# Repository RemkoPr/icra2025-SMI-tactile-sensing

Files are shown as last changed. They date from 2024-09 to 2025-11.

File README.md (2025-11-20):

# ICRA2025: Self-Mixing Laser Interferometry for Robotic Tactile Sensing

[[Main Paper](https://arxiv.org/abs/2502.15390), [Follow-up](https://arxiv.org/abs/2504.13711)] The source files in this repo are provided as-is, additional support for recreating the design can be requested, see contact information below.

# Repo structure

`code > arduino` contains readout firmware for the fingertips. In the paper, the SMI fingertip was read by an Arduino UNO or our [Halberd coupling](https://github.com/RemkoPr/airo-halberd/tree/main), the microphone was read by an Arduino MKR 1000 WiFi.

`code > python` contains code to communicate with the readout microcontrollers from a remote machine over a serial connection.

`data` contains the data files used in the paper.

`mechanical-design` contains SolidWorks design files for the structural parts of the fingertips.

`pcb-design` contains KiCad design files for the PCBs.

For the spectrogram classificatier used in the [follow-up paper](https://arxiv.org/abs/2504.13711), see [this repo](https://github.com/tlpss/ast).

# User Guide

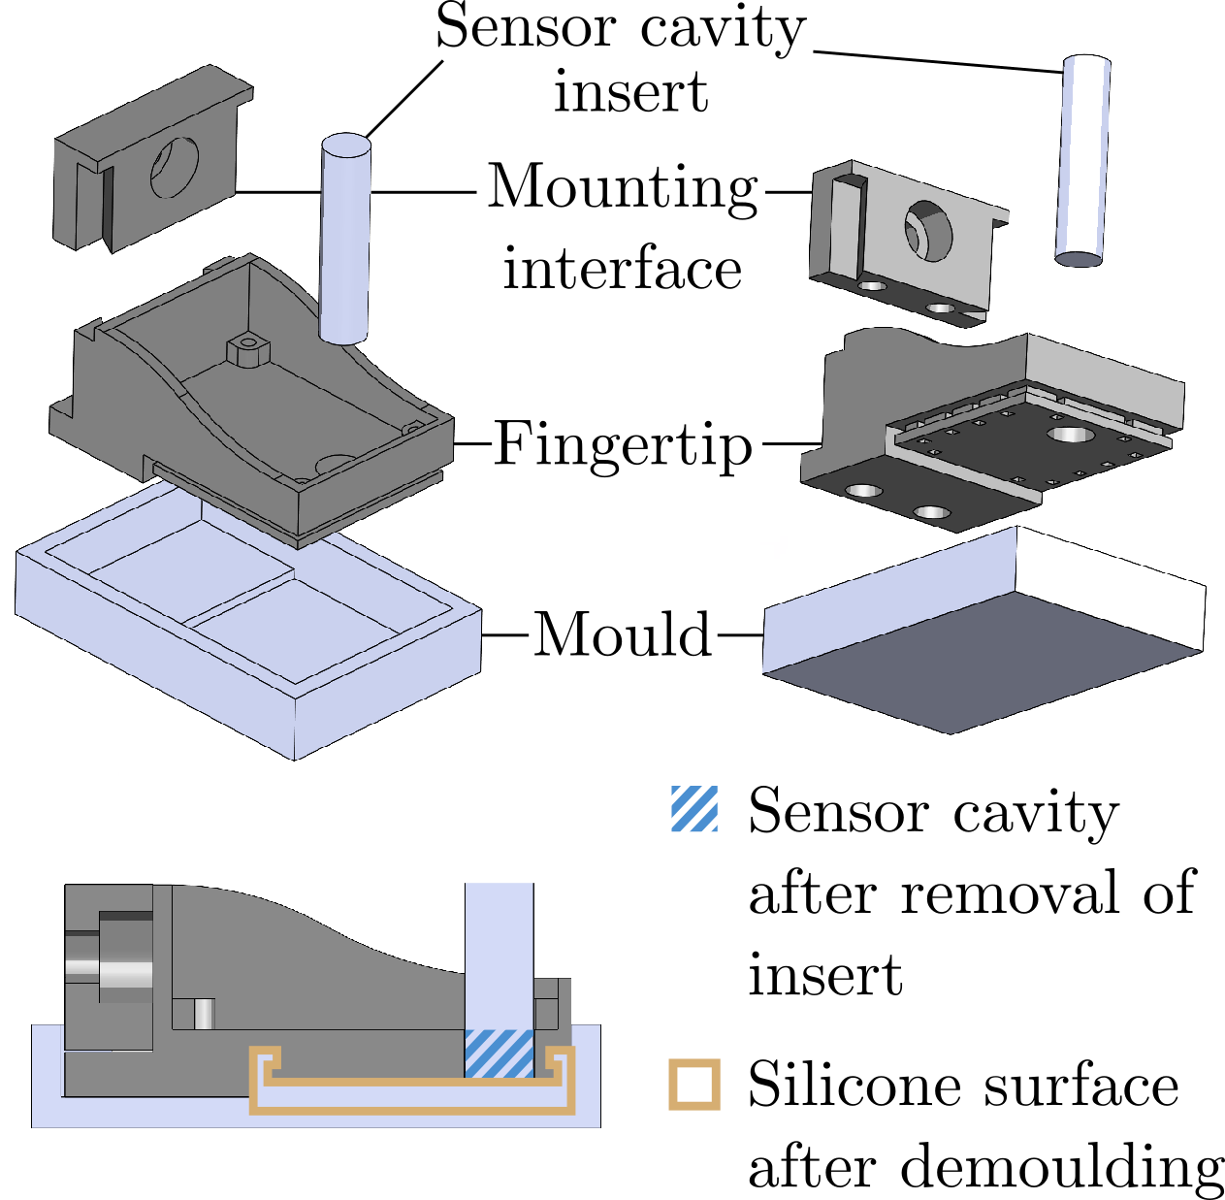
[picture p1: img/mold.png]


The info in this paragraph is relevant for both the microphone and the laser.

Order the PCBs (`pcb-design > microphone` and `pcb-design > laser`) from your favorite manufacturer, refer to the BOM in the main directory of this repo for required parts.
Print the .stl files in `mechanical-design`.
The process of moulding the silicone contact surface is illustrated by the graphic on the right. To keep the "sensor cavity insert" in the right position, fix it with hot glue. It is recommended to attach the "mounting interface" to the fingertip while curing, so that the silicone has less chance to leak.

<BR CLEAR="all">

## Microphone specifics

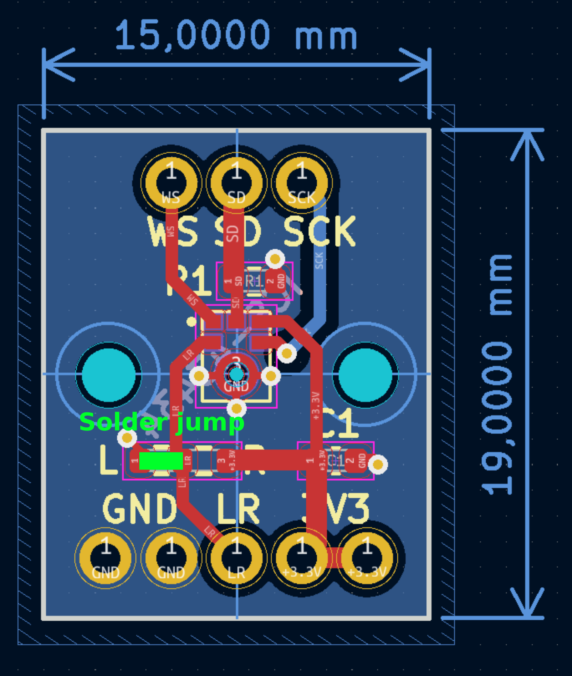
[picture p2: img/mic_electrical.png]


On the PCB, you must set the microphone to either by left or right channel, this will determine during which phase of the I2S communication cycle the microphone sends its data. Do this by soldering a bridge as indicated on the image (the readout code in this repo was tested for left channel, so with a bridge soldered from the middle pad to the L pad).

The MKR1000 firmware (`code > arduino > microphone`) was used for the paper, the wiring is explained in the top rows of the `I2S_MKR1000.ino` file. The `I2S_ArduinoNanoBLE_16kHz` is a first attempt at a readout implementation for the Arduino Nano 33 BLE, for which the standard I2S library isn't implemented.

To run the Python code (`code > python`), run `python -m code.python.communication.readers.micmanip_serial_reader`. The data is published to a CycloneDDS topic MicManip. You can visualise it using `python -m code.python.visualisation.visualisers.micmanip_spectrogram_visualiser MicManip`
<BR CLEAR="all">

## Laser specifics

⚠️ The SMI circuit has a ~5 min warmup time before microvibrations can be measured.

The readout frequency when read with an Arduino UNO was 3.7kHz, and 18kHz with our [Halberd coupling](https://github.com/RemkoPr/airo-halberd/tree/main) (or equivalently with an Arduino Nano 33 BLE, same microcontroller unit). When using higher readout frequency, turn off the 2kHz anti-aliasing filter with the on-PCB slide switch.

To run the Python code (`code > python`), run `python -m code.python.communication.readers.laserslip_serial_reader`. The data is published to a CycloneDDS topic LaserSlip. You can visualise it using `python -m code.python.visualisation.visualisers.laserslip_spectrogram_visualiser LaserSlip`

# Contact

For support regarding the design files in this repo, raise an issue or contact me at remko.proesmans@ugent.be.

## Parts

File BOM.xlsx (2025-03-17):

Mechanical | Qty per fingertip | Purpose
3D filament (e.g. PLA) |  | Mechanical parts
Castable Silicone 50A hardness (e.g. Silicone Addition colorless 50 by Silicones and More) |  | Silicone contact surface
M3 threaded heat-set inserts | 2 | Inserted into the mounting interface
M5x14 bolt | 1 | Mounting fingertip to Robotiq gripper
M2x6 bolts | 4 | Attaching PCBs to printed fingertips
Electrical | Qty per fingertip | Item | PCB designation
Microphone
ICS43434 | 1 | Microphone
100 nF 0603 capacitor | 1
100 kOhm 0603 resistor | 1
Laser
ADL-65075TL | 1 | Laser | D1
ncr320zx | 1 | Constant current source | Q1
ADA4000-1 | 3 | Amplifiers and filters | TIA1, SA1, AA1
MCP3201-BI/SN | 1 | ADC | ADC1
MCP1541T-I_TT | 1 | ADC reference voltage | U2
JS202011SCQN | 1 | Switch | S1
TPS7A3901DSCR | 1 | Voltage regulator | LDO1
MEA1D2409SC | 1 | Voltage regulator | U3
82223C | 2 | 22 µH inductor | L1, L2
5 pF 0603 capacitor | 1 | TIA gain stabilising | C1
100 nF 0603 capacitor | 10 |  | C2, C3, C7, C8, C9, C10, C13, C14, C15, C19
1 µF 0603 capacitor | 1 |  | C20
2,2 µF 0603 capacitor | 3 |  | C4, C5, C6
10 µF 0603 capacitor | 4 |  | C11, C12, C16, C17
500 Ohm 0603 resistor | 1 |  | R5
800 Ohm 0603 resistor | 2 |  | R9, R10
6,8 kOhm 0603 resistor | 1 |  | R4
10 kOhm 0603 resistor | 3 |  | R3, R13, R14
15 kOhm 0603 resistor | 1 |  | R6
32,4 kOhm 0603 resistor | 1 |  | R7
39 kOhm 0603 resistor | 1 | TIA gain | R2
42,2 kOhm 0603 resistor | 1 |  | R8

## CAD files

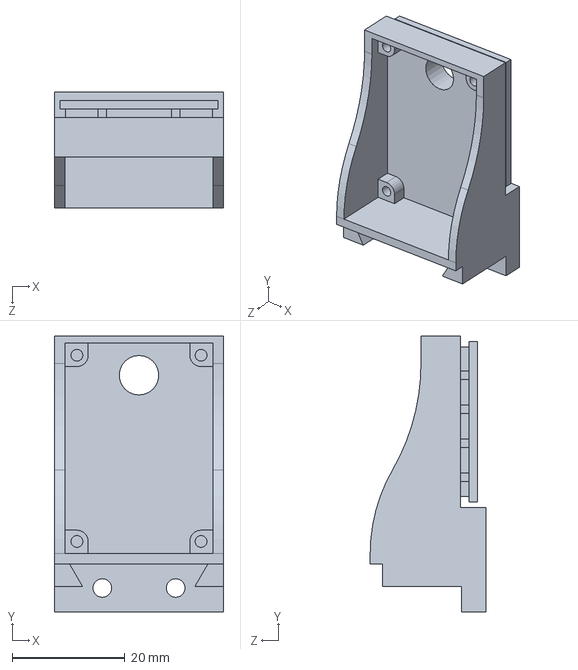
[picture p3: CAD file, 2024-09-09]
mechanical-design/laser/fingertip.SLDPRT
30.0 x 48.9 x 20.5 mm

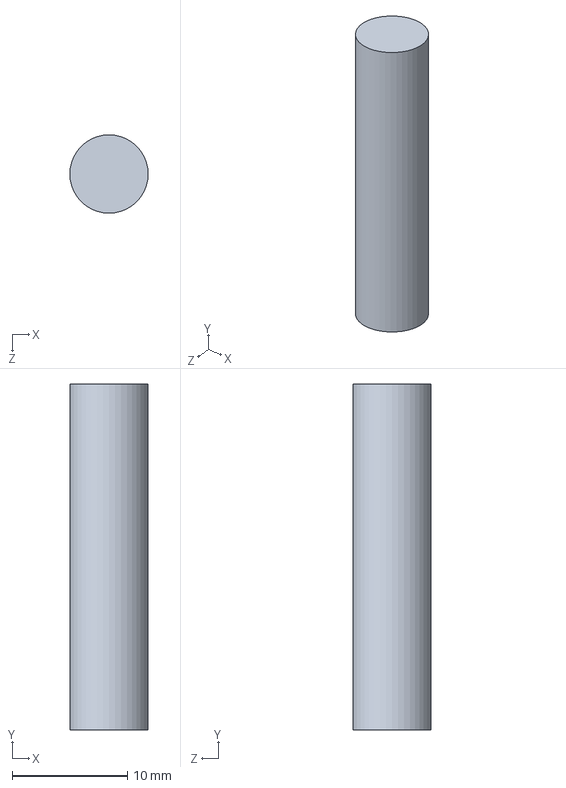
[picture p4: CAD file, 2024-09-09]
mechanical-design/laser/sensor_cavity_insert.SLDPRT
6.80 x 30.0 x 6.80 mm

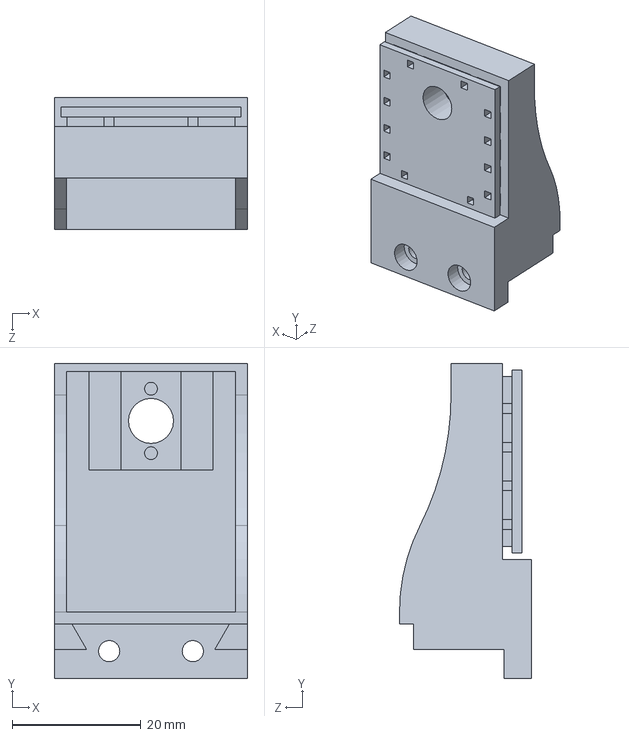
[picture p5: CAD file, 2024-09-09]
mechanical-design/microphone/fingertip.SLDPRT
30.0 x 48.9 x 20.5 mm

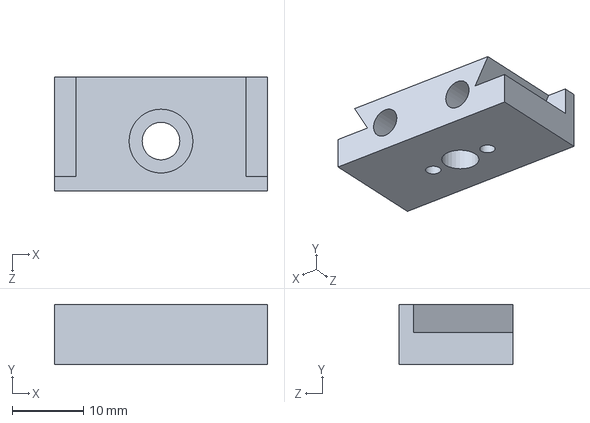
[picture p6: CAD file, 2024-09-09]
mechanical-design/laser/mounting_interface.SLDPRT
30.0 x 8.50 x 16.0 mm

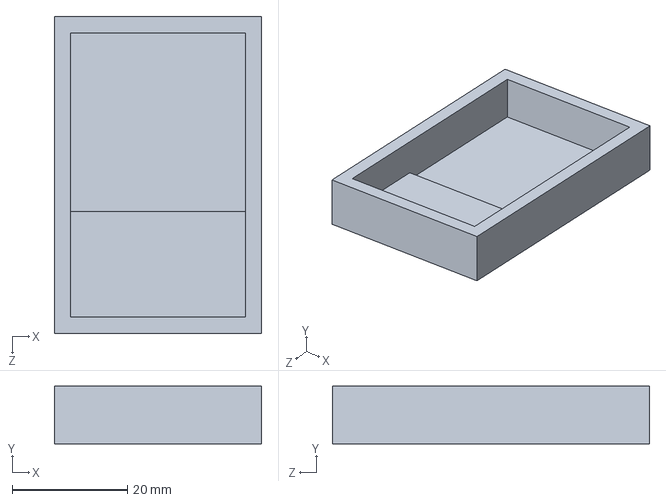
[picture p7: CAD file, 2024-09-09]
mechanical-design/laser/mould.SLDPRT
36.0 x 10.0 x 55.0 mm

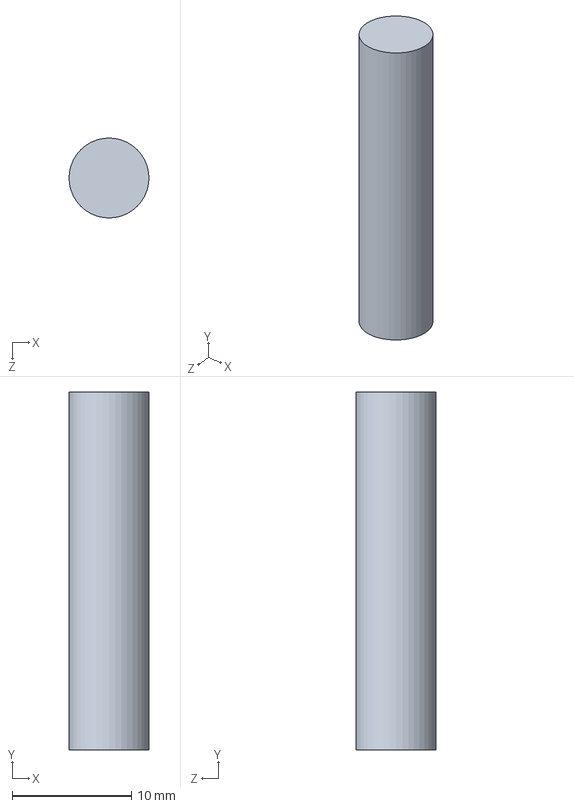
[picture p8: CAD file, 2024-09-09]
mechanical-design/microphone/sensor_cavity_insert.SLDPRT
6.70 x 30.0 x 6.70 mm

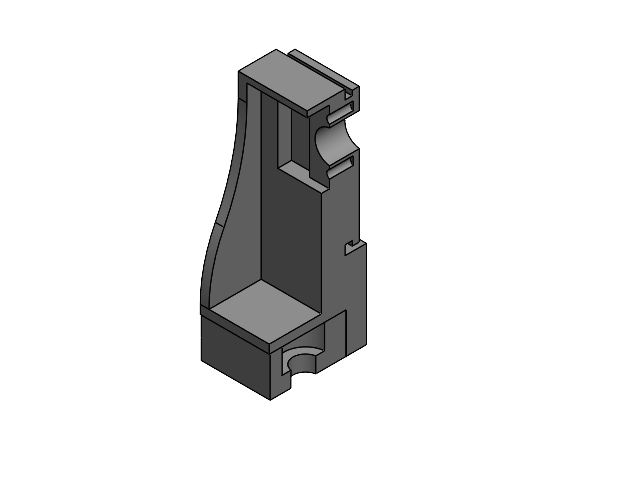
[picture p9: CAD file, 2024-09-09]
mechanical-design/microphone/assembly.SLDASM
fingertip_silicone
base

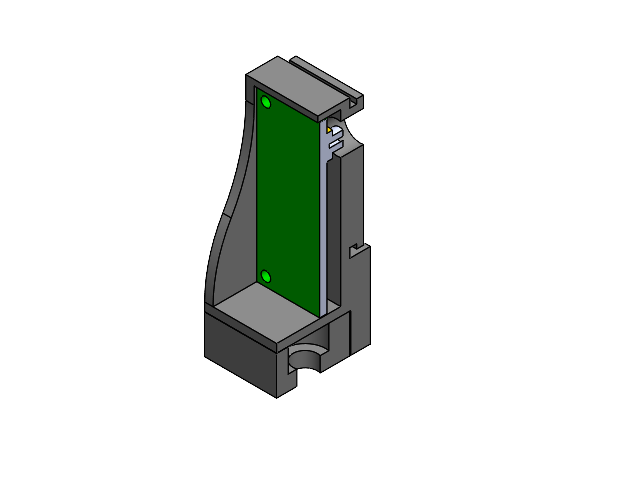
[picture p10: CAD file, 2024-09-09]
mechanical-design/laser/assembly.SLDASM
fingertip
base
PCB

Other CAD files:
mechanical-design/microphone/mounting_interface.SLDPRT
mechanical-design/microphone/mould.SLDPRT
mechanical-design/laser/fingertip.STL
mechanical-design/laser/mould.STL
mechanical-design/laser/mounting_interface.STL
mechanical-design/laser/sensor_cavity_insert.STL
mechanical-design/microphone/fingertip.STL
mechanical-design/microphone/mould.STL
mechanical-design/microphone/mounting_interface.STL
mechanical-design/microphone/sensor_cavity_insert.STL

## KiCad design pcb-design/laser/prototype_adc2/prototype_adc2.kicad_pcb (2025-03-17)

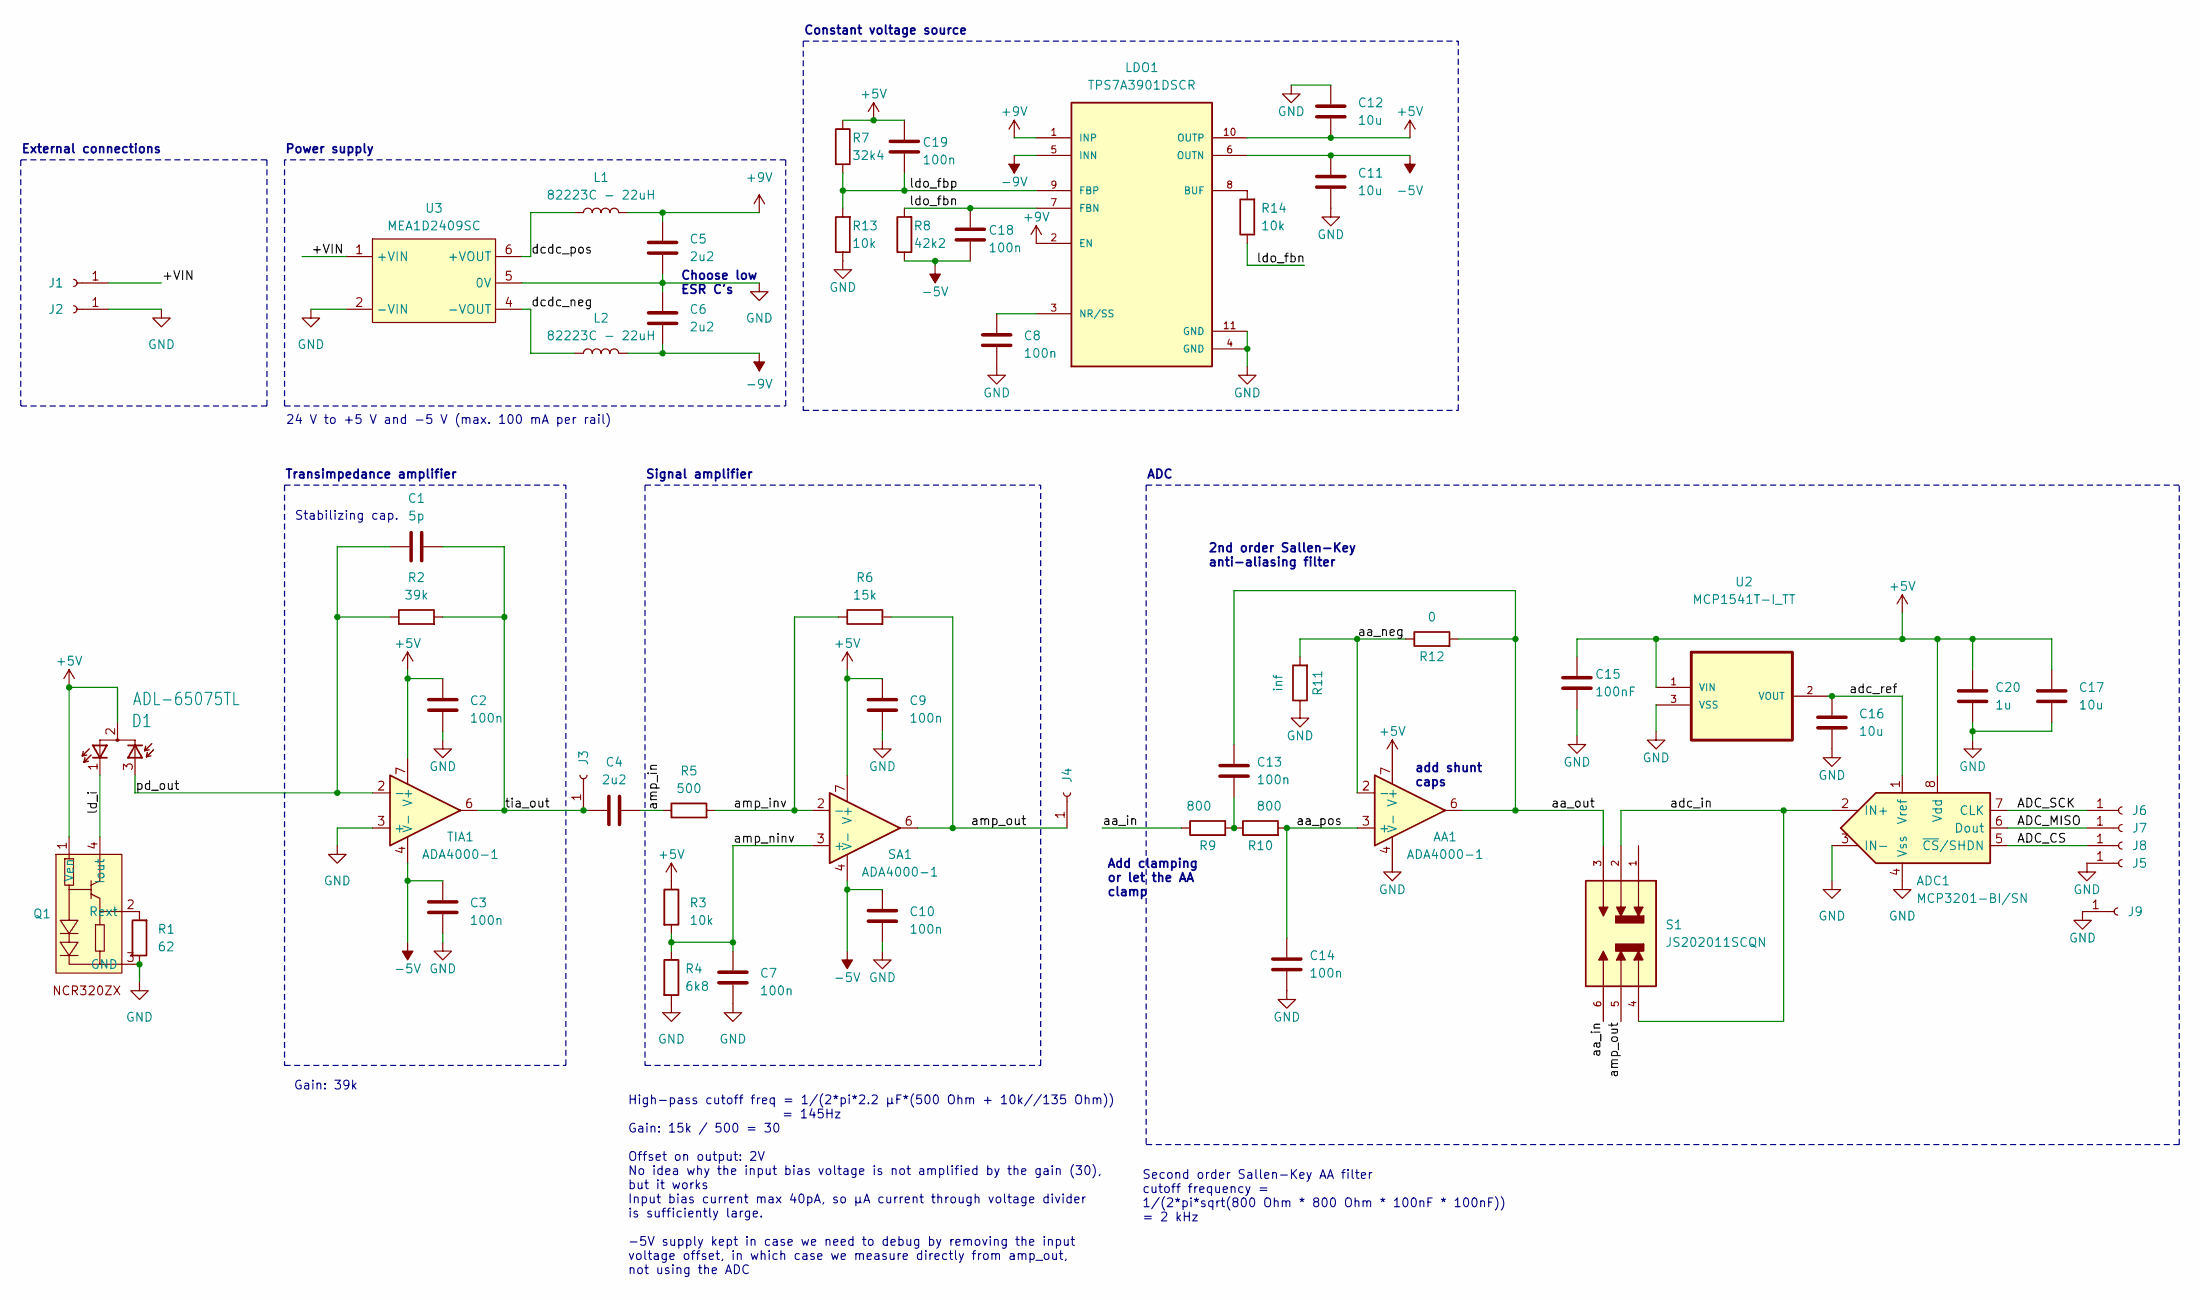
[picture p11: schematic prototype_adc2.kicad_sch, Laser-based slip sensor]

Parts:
AA1: ADA4000-1; ada4000-SOIC127P600X175-8N
ADC1: MCP3201-BI/SN; SOIC127P600X175-8N
C1: 5p; C_0603_1608Metric
C2, C3, C7, C8, C9, C10, C13, C14, C18, C19: 100n; C_0603_1608Metric
C4, C5, C6: 2u2; C_0603_1608Metric
C11, C12, C16, C17: 10u; C_0603_1608Metric
C15: 100nF; C_0603_1608Metric
C20: 1u; C_0603_1608Metric
D1: ADL-65075TL; TO18L
J1, J2, J3, J4, J5, J6, J7, J8, J9: Conn_01x01_Socket; HOLE
L1, L2: 82223C - 22uH; 8200
LDO1: TPS7A3901DSCR; SON50P300X300X80-11N
Q1: TRANS_BCP56-16TX
R1: 62; R_0603_1608Metric
R2: 39k; R_0603_1608Metric
R3, R13, R14: 10k; R_0603_1608Metric
R4: 6k8; R_0603_1608Metric
R5: 500; R_0603_1608Metric
R6: 15k; R_0603_1608Metric
R7: 32k4; R_0603_1608Metric
R8: 42k2; R_0603_1608Metric
R9, R10: 800; R_0603_1608Metric
R11: inf; R_0603_1608Metric
R12: 0; R_0603_1608Metric
S1: JS202011SCQN; SW_JS202011SCQN
SA1: ADA4000-1; ada4000-SOIC127P600X175-8N
TIA1: ADA4000-1; ada4000-SOIC127P600X175-8N
U2: MCP1541T-I_TT; SOT96P237X112-3N
U3: MEA1D2409SC

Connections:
+5V: AA1.7 (V+), ADC1.8 (Vdd), C2.1, C9.1, C12.2, C15.1, C17.1, C19.1, C20.1, D1.2 (CMONI), LDO1.10 (OUTP), Q1.1 (Ven), R3.1, R7.1, SA1.7 (V+), TIA1.7 (V+), U2.1 (VIN)
+9V: C5.1, L1.2, LDO1.1 (INP), LDO1.2 (EN)
-5V: C3.1, C10.1, C11.1, C18.2, LDO1.6 (OUTN), R8.1, SA1.4 (V-), TIA1.4 (V-)
-9V: C6.2, L2.2, LDO1.5 (INN)
/+VIN: J1.1, U3.1 (+VIN)
/ADC_CS: ADC1.5 (~CS/SHDN), J8.1
/ADC_MISO: ADC1.6 (Dout), J7.1
/ADC_SCK: ADC1.7 (CLK), J6.1
/aa_in: R9.1, S1.6
/aa_neg: AA1.2 (-), R11.2, R12.1
/aa_out: AA1.6, C13.1, R12.2, S1.3
/aa_pos: AA1.3 (+), C14.1, R10.2
/adc_in: ADC1.2 (IN+), S1.2, S1.4
/adc_ref: ADC1.1 (Vref), C16.1, U2.2 (VOUT)
/amp_in: C4.2, R5.1
/amp_inv: R5.2, R6.1, SA1.2 (-)
/amp_ninv: C7.1, R3.2, R4.1, SA1.3 (+)
/amp_out: J4.1, R6.2, S1.5, SA1.6
/dcdc_neg: L2.1, U3.4 (-VOUT)
/dcdc_pos: L1.1, U3.6 (+VOUT)
/ld_i: D1.1 (C), Q1.4 (Iout)
/ldo_fbn: C18.1, LDO1.7 (FBN), R8.2, R14.1
/ldo_fbp: C19.2, LDO1.9 (FBP), R7.2, R13.2
/pd_out: C1.1, D1.3 (A), R2.1, TIA1.2 (-)
/tia_out: C1.2, C4.1, J3.1, R2.2, TIA1.6
GND: AA1.4 (V-), ADC1.3 (IN-), ADC1.4 (Vss), C2.2, C3.2, C5.2, C6.1, C7.2, C8.2, C9.2, C10.2, C11.2, C12.1, C14.2, C15.2, C16.2, C17.2, C20.2, J2.1, J5.1, J9.1, LDO1.4 (GND), LDO1.11 (GND), Q1.3 (GND), R1.1, R4.2, R11.1, R13.1, TIA1.3 (+), U2.3 (VSS), U3.2 (-VIN), U3.5 (0V)
unnamed: C13.2, R9.2, R10.1
unnamed: LDO1.8 (BUF), R14.2
unnamed: C8.1, LDO1.3 (NR/SS)
unnamed: Q1.2 (Rext), R1.2

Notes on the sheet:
ADC
Add clamping or let the AA clamp
Second order Sallen-Key AA filter cutoff frequency = 1/(2*pi*sqrt(800 Ohm * 800 Ohm * 100nF * 100nF)) = 2 kHz
2nd order Sallen-Key anti-aliasing filter
High-pass cutoff freq = 1/(2*pi*2.2 µF*(500 Ohm + 10k//135 Ohm)) = 145Hz Gain: 15k / 500 = 30 Offset on output: 2V No idea why the input bias voltage is not amplified by the gain (30), but it works Input bias current max 40pA, so µA current through voltage divider is sufficiently large. -5V supply 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
Gain: 39k
24 V to +5 V and -5 V (max. 100 mA per rail)
Stabilizing cap.
External connections
Signal amplifier
Transimpedance amplifier
add shunt caps
Constant voltage source
Power supply
Choose low ESR C's

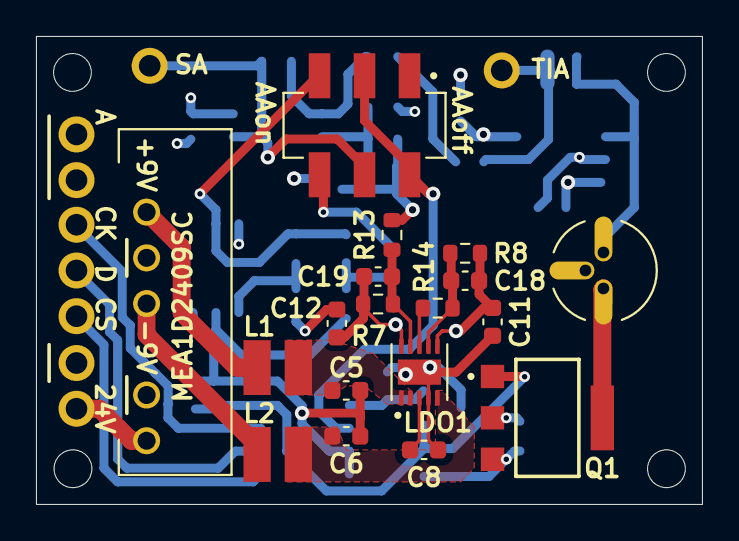
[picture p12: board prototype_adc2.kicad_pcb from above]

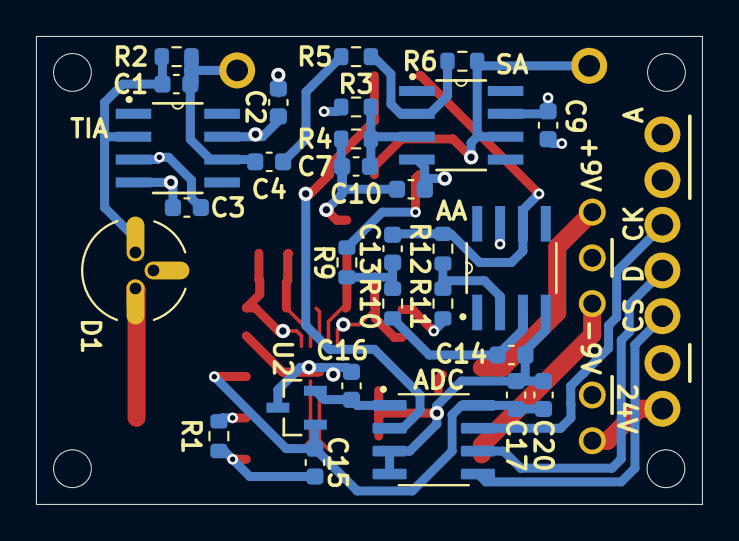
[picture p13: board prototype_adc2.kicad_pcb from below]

Board: 4 copper layers, 37.0 x 26.0 mm, 55 parts (29 on the bottom side), 30 nets.

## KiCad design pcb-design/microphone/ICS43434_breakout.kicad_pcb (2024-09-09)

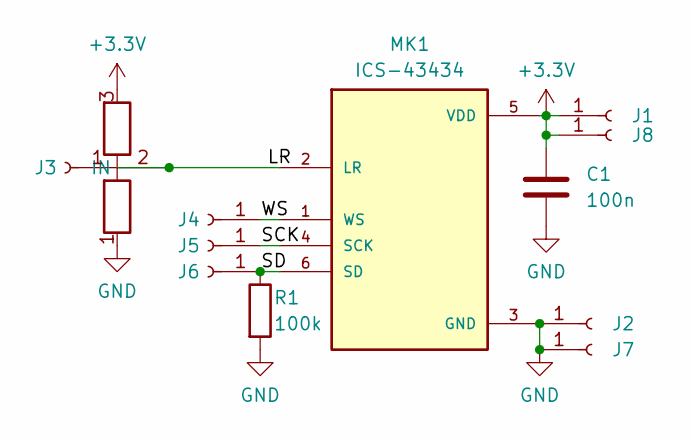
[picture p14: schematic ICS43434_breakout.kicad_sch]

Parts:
C1: 100n; C_0603_1608Metric
J1, J2, J3, J4, J5, J6, J7, J8: Conn_01x01_Socket; HOLE
MK1: ICS-43434; MIC_ICS-43434
R1: 100k; R_0603_1608Metric
U1: ADDR_SELECT

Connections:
+3.3V: C1.1, J1.1, J8.1, MK1.5 (VDD), U1.3; also elsewhere on the board
/LR: J3.1, MK1.2 (LR), U1.2 (IN); also elsewhere on the board
/SCK: J5.1, MK1.4 (SCK); also elsewhere on the board
/SD: J6.1, MK1.6 (SD), R1.1; also elsewhere on the board
/WS: J4.1, MK1.1 (WS); also elsewhere on the board
GND: C1.2, J2.1, J7.1, MK1.3 (GND), R1.2, U1.1; also elsewhere on the board

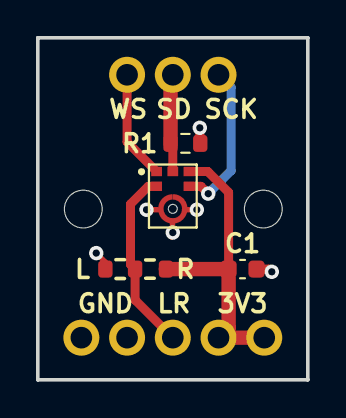
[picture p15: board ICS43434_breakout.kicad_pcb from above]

Board: 2 copper layers, 15.0 x 19.0 mm, 12 parts (0 on the bottom side), 6 nets.

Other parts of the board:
ICS-43434: ICS-43434; MIC_ICS-43434

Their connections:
+3.3V: ICS-43434.5 (VDD); also elsewhere on the board
/LR: ICS-43434.2 (LR); also elsewhere on the board
/SCK: ICS-43434.4 (SCK); also elsewhere on the board
/SD: ICS-43434.6 (SD); also elsewhere on the board
/WS: ICS-43434.1 (WS); also elsewhere on the board
GND: ICS-43434.3 (GND); also elsewhere on the board

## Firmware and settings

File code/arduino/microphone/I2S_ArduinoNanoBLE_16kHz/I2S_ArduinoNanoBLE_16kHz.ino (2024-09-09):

  /*
 * SOURCE:
 * https://forum.arduino.cc/t/i2s-wav-playback-on-nrf52840/1058134
 * https://jimmywongiot.com/2021/06/26/i2c-mems-microphone-with-nordic-nrf52-series/
 * https://github.com/gregtomasch/nRF52_24-bit-_I2S_Microphone_Audio_Recording_Utility/blob/729c85e05485d0dac77a24e3e650015ecd7c4914/i2s_Slave_External_PWM_CK_Mono/main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
 * 
 * 
 * Implementation with own I2S clocks using PWM, better readout attempt:
 * sck and sdin are logged while WS low (left channel), "dead time" while WS high is used to 
 * extract a value from the logs
 * 
 */

#include <nrfx_i2s.h> // or #include <hal/nrf_i2s.h>
#include <nrfx_pwm.h>


#define PIN_SCK     D10                 // BCLK/SCK
#define PIN_LRCK    D9                 // WS/LRCK
#define PIN_SDIN    D7                 // DIN
#define BUFFER_LEN  49*32   // 64 MHz clock frequency, SCK of ~1.3MHz. 32 SCK cycles must be stored,
                            // at the very most 49 MCU clock cycles per SCK cycle, so 49*32. Measurements 
                            // show nothing above 139, most of the time its 73


uint8_t data[3];
uint32_t buffer_ctr = 0;
uint8_t sck_buffer[BUFFER_LEN] = {0};
uint8_t sdin_buffer[BUFFER_LEN] = {0};
//uint32_t buffer_ctr_ctr = 0;
//uint32_t buffer_ctr_buffer[100] = {0};
int32_t currentValue = 0;
int bit_ctr = 31;
int sample_ctr = 0;
int t_start = micros();

static nrfx_pwm_t pwm1 = NRFX_PWM_INSTANCE(0);
static nrfx_pwm_t pwm2 = NRFX_PWM_INSTANCE(1);

static nrf_pwm_values_individual_t seq1_values[] = {3};

static nrf_pwm_sequence_t seq1 = {
    .values = {
        .p_individual = seq1_values
    },
    .length          = NRF_PWM_VALUES_LENGTH(seq1_values),
    .repeats         = 1,
    .end_delay       = 0
};

nrfx_pwm_config_t config1 = {
    .output_pins  = {
        32 + 8, // Arduino Nano 33 BLE pin D12, SCK source
        NRFX_PWM_PIN_NOT_USED,
        NRFX_PWM_PIN_NOT_USED,
        NRFX_PWM_PIN_NOT_USED,
    },
    .irq_priority = 7,
    .base_clock   = (nrf_pwm_clk_t)(1UL),  //NRF_PWM_CLK_8MHz,
    .count_mode   = NRF_PWM_MODE_UP,
    .top_value    = 6,
    .load_mode    = NRF_PWM_LOAD_INDIVIDUAL,
    .step_mode    = NRF_PWM_STEP_AUTO,
};
nrfx_pwm_config_t config2 = {
    .output_pins  = {
        32 + 1, // Arduino Nano 33 BLE pin D11, WS source
        NRFX_PWM_PIN_NOT_USED,
        NRFX_PWM_PIN_NOT_USED,
        NRFX_PWM_PIN_NOT_USED,
    },
    .irq_priority = 7,
    .base_clock   = (nrf_pwm_clk_t)(7UL),  //NRF_PWM_CLK_125kHz,
    .count_mode   = NRF_PWM_MODE_UP,
    .top_value    = 6,
    .load_mode    = NRF_PWM_LOAD_INDIVIDUAL,
    .step_mode    = NRF_PWM_STEP_AUTO,
};


void setup() {

  Serial.begin(115200);
  while (!Serial) { delay(10); }
  
  // PWM setup for spoofed BCLK/SCK and WS/LRCK
  nrfx_pwm_init(&pwm1, &config1, NULL);
  nrfx_pwm_init(&pwm2, &config2, NULL);

  nrfx_pwm_simple_playback(&pwm1, &seq1, 1, NRFX_PWM_FLAG_LOOP);
  nrfx_pwm_simple_playback(&pwm2, &seq1, 1, NRFX_PWM_FLAG_LOOP);
  pinMode(PIN_SCK, INPUT);
  pinMode(PIN_LRCK, INPUT);
  pinMode(PIN_SDIN, INPUT);

  for(int i=0 ; i < 9; i++) {
    Serial.write((byte)0);
  }
}

void loop() {
  if (!((NRF_P0->IN >> 27))) { // WS already low, wait out this cycle
    while(!((NRF_P0->IN >> 27)));
    // WS turns high, nothing interesting happens here, we have some time to get out of this "if"
  }
  
  while((NRF_P0->IN >> 27)); // WS known to be high, wait for it to turn low
  
  // WS just turned low, immediately log
  sck_buffer[buffer_ctr] = NRF_P1->IN >> 2;
  sdin_buffer[buffer_ctr] = NRF_P0->IN >> 23;
  buffer_ctr++;
  int port0 = NRF_P0->IN;
  while(!(port0 >> 27)) { // keep logging while WS remains low
    sck_buffer[buffer_ctr] = NRF_P1->IN >> 2;
    sdin_buffer[buffer_ctr] = port0 >> 23;
    buffer_ctr++;
    port0 = NRF_P0->IN;
  }
  
  // WS turned high again, some time for processing
  bool sck_high = false;
  for(int i = 0; i < buffer_ctr; i++) {
    if(sck_buffer[i] & !sck_high) { // rising sck edge
      sck_high = true;
    } else if(!sck_buffer[i] & sck_high) { // falling sck edge
      sck_high = false;
      currentValue |= sdin_buffer[i] << bit_ctr;
      bit_ctr--;
    }
  }
  //Serial.println("value: " + String(currentValue >> 8) + "\t bit ctr: " + String(bit_ctr));
  if(bit_ctr == 0) {
    //Serial.println(currentValue >> 8);
    /*Serial.write(currentValue >> 24);
    Serial.write(currentValue >> 16);
    Serial.write(currentValue >> 8);*/
    sample_ctr++;
  }
  currentValue = 0;
  bit_ctr = 31;
  buffer_ctr = 0;
  if(sample_ctr > 5000) {
    Serial.println( sample_ctr/((micros() - t_start)/1000000.0) );
    t_start = micros();
    sample_ctr = 0;
  }
}

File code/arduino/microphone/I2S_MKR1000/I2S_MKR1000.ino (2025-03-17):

/*
 This example reads audio data from an Invensense's ICS43432 I2S microphone
 breakout board, and prints out the samples to the Serial console. The
 Serial Plotter built into the Arduino IDE can be used to plot the audio
 data (Tools -> Serial Plotter)

 Circuit:
 * Arduino/Genuino Zero, MKR family and Nano 33 IoT
 * ICS43432:
   * GND connected GND
   * 3.3V connected to VCC
   * WS connected to pin D3
   * SCK connected to pin D2
   * SD connected to pin A6

 created 17 November 2016
 by Sandeep Mistry 
 adapted 2024
 by Remko Proesmans
 */

#include <I2S.h>

#define DEBUG false

#define FS  20000 
#define SAMPLE_BUFFER_LEN   50
#define SAMPLE_BYTE_LEN     3

int start_time_ = micros();
int time_passed = 0;
uint8_t sample_buffer[SAMPLE_BUFFER_LEN * SAMPLE_BYTE_LEN] = {0};
int sample_ctr = 0;

void setup() {
  Serial.begin(115200);
  while (!Serial);

  // start I2S at 8 kHz with 32-bits per sample
  if (!I2S.begin(I2S_PHILIPS_MODE, FS, 32)) {
    Serial.println("Failed to initialize I2S!");
    while (1); // do nothing
  }
  
  delay(5000);
}

void loop() {
  int32_t sample = I2S.read();

#if DEBUG
  time_passed = micros() - start_time_;
  if (time_passed > 1000000) {
    Serial.print("Readout frequency: ");
    Serial.println(sample_ctr/(time_passed/1000000.0));
    start_time_ = micros();
    sample_ctr = 0;
  }
#endif

  if (sample) {
#if DEBUG
    Serial.println("x: " + String(sample) + " -> " + String(sample >> 8));
#endif
    sample_buffer[sample_ctr*SAMPLE_BYTE_LEN] = sample >> 24;
    sample_buffer[sample_ctr*SAMPLE_BYTE_LEN + 1] = (sample >> 16) & 0xFF;
    sample_buffer[sample_ctr*SAMPLE_BYTE_LEN + 2] = (sample >> 8) & 0xFF;

    sample_ctr++;
  }
  if(sample_ctr == SAMPLE_BUFFER_LEN) {
    sample_ctr = 0;

#if DEBUG
    Serial.println("------------------------------------------");
    for(int i=0 ; i < SAMPLE_BUFFER_LEN ; i++) {
      Serial.println(String(sample_buffer[i*SAMPLE_BYTE_LEN]) + " " 
                    + String(sample_buffer[i*SAMPLE_BYTE_LEN + 1]) + " " 
                    + String(sample_buffer[i*SAMPLE_BYTE_LEN + 2]));
    }
    Serial.println("------------------------------------------");
#else
    Serial.write(sample_buffer, SAMPLE_BUFFER_LEN*SAMPLE_BYTE_LEN);
#endif
  }
}

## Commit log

2024-09-09 inital push
    [ICS43434_breakout.kicad_pcb, ICS43434_breakout.kicad_sch, assembly.SLDASM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]
2025-02-19 added motor noise data files and plotting notebook
    [motor_1000_v2.csv, motor_500_v2.csv, motor_750_v2.csv]
2025-02-27 structure plotting notebook better
    [bolts_laser1.csv, bolts_laser2.csv, bolts_laser3.csv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]
2025-02-27 added stepper motor plot to notebook
2025-03-17 renamed mechanical cad files to align with moulding image
    [mould.SLDPRT, mould.STL, mounting_interface.SLDPRT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]
2025-03-17 laser schematic AA cutoff fix
    [prototype_adc2-B_Cu.gbl, prototype_adc2-B_Mask.gbs, prototype_adc2-B_Paste.gbp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]
2025-03-17 added BOM
    [BOM.xlsx]
2025-03-17 fixed laser footprint on pcb
    [prototype_adc2-B_Cu.gbl, prototype_adc2-B_Mask.gbs, prototype_adc2-B_Paste.gbp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]
